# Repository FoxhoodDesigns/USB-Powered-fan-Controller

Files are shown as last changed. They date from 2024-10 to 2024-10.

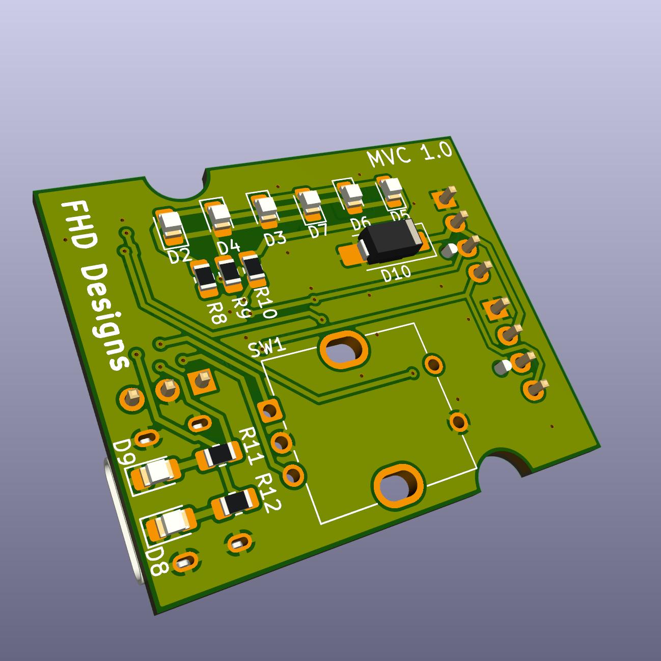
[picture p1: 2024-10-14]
KiCad/MVC.jpg

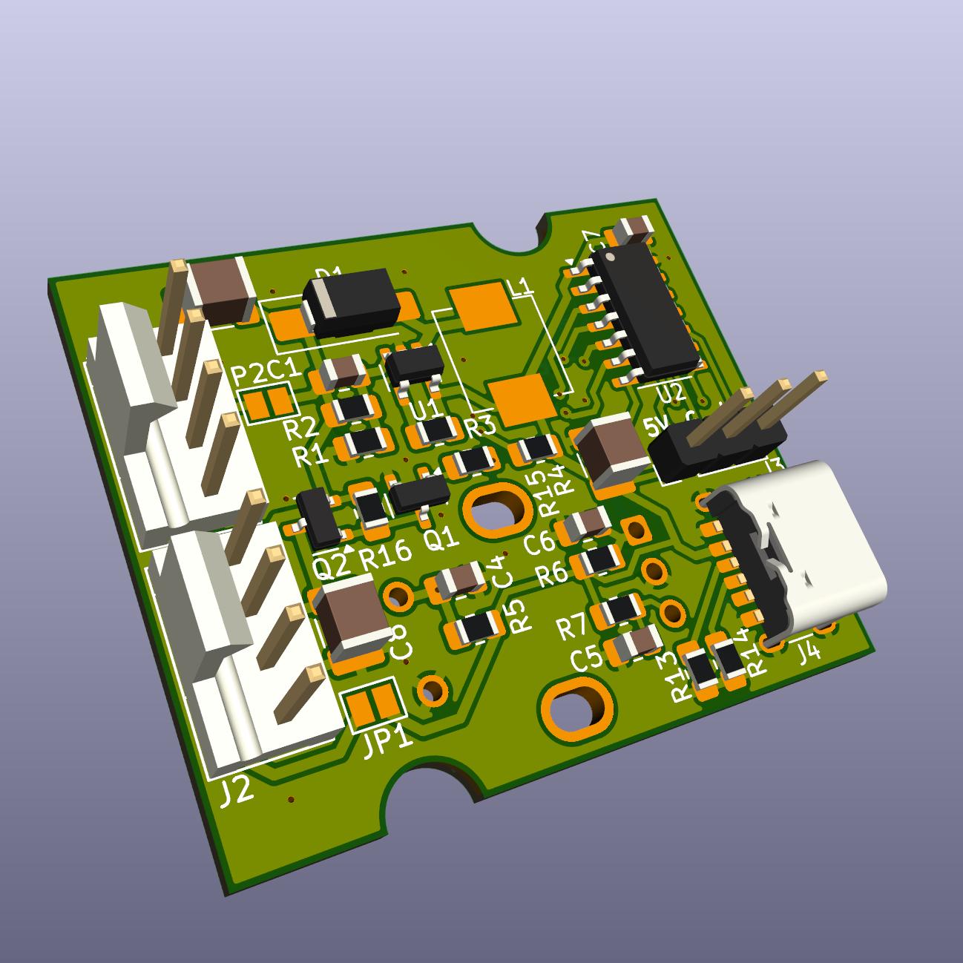
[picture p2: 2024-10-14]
KiCad/MVCfront.jpg

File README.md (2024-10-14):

# USB-Powered-fan Controller
This small device is designed to allow one to power and control a 12V (case)fan from a standard 5V 1A USB charger.
Intended application are small DIY fan projects such as a Desktop fan using a Noctua NV-AA1-12, Fume Extracters and Part cooling.
## Overal design:
The controller can be divided into four parts:
- A 5V->12V Boost converter based on a LMR62421XMF reference design
- A Load switch using a PMV50PEAR and a BSS138.
- A ATTiny414 that is handling PWM generation and I/O
- The I/O itself consisting of (charlieplexed) leds, Encoder, USB-C port and two 4-pin FAN pinouts
## Working
On power-up the controller will try to spin up the fan to about half speed via a 25Khz PWM signal, measure the RPM, set PWM to 80% and check if there was significant change.
If there was, then it assumes the FAN is PWM compatible and keep to using PWM, if not it will assume the FAN is DC and instead starts pulsing the Load Switch.

During operation one can set the speed of the fan anywhere between 40 and 100 percent. Pressing the encoder SW causes the controller to halt the fan till pressed again

If during operation the FAN either halts OR speeds up too much (wip), the controller will immediately shut off power and remain locked till it got power-cycled as a protection measure against sudden jamming/defects.

### TODO:
- Gerber upload
- Overhaul the code and implement a speed up detection test.
- Test with other fans.
- BOM upload
- Potentially setting up for manufacturing by PCBWay/JLCPCB
- Verify if possible to program via AVRDUDE using CH340

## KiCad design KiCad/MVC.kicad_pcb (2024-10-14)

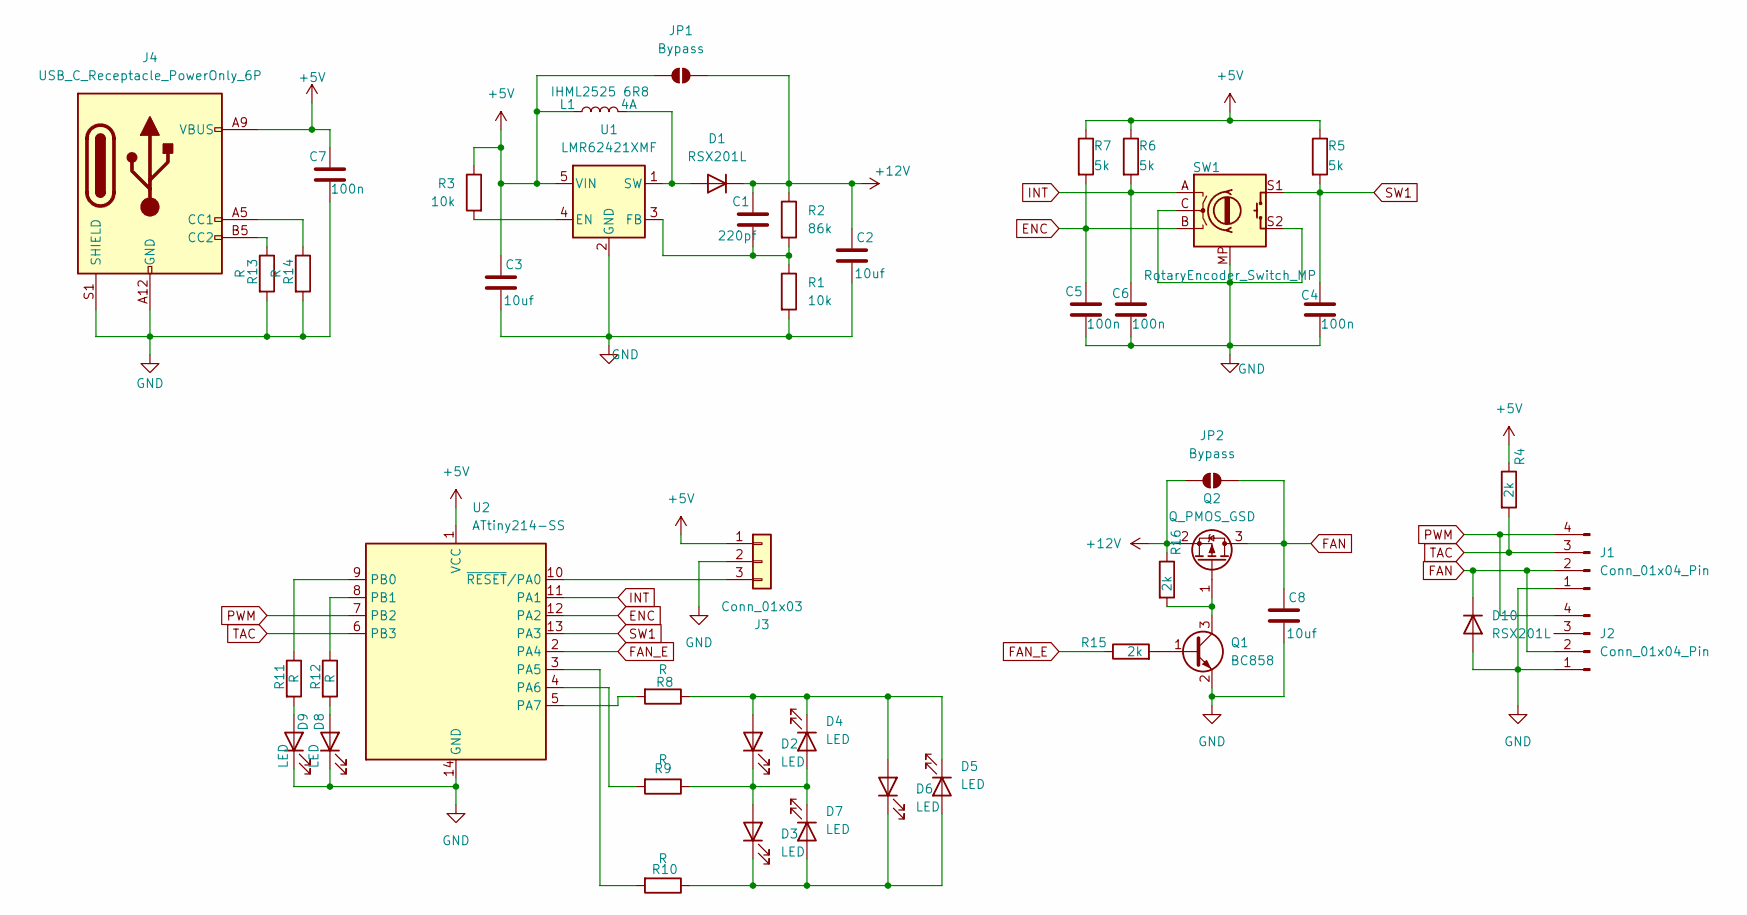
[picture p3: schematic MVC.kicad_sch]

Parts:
C1: 220pf; C_0805_2012Metric_Pad1.18x1.45mm_HandSolder; Voltage 1kV; Tolerance 100%
C2, C3, C8: 10uf; C_1210_3225Metric_Pad1.33x2.70mm_HandSolder; Voltage 1kV; Tolerance 100%
C4, C5, C6, C7: 100n; C_0805_2012Metric_Pad1.18x1.45mm_HandSolder; Voltage 1kV; Tolerance 100%
D1, D10: RSX201L; D_SMA_Handsoldering
D2, D3, D4, D5, D6, D7, D8, D9: LED; LED_0805_2012Metric_Pad1.15x1.40mm_HandSolder
J1, J2: Conn_01x04_Pin; FanPinHeader_1x04_P2.54mm_Vertical
J3: Conn_01x03; PinHeader_1x03_P2.54mm_Vertical
J4: USB_C_Receptacle_PowerOnly_6P; USB_C_Receptacle_GCT_USB4125-xx-x_6P_TopMnt_Horizontal
JP1, JP2: Bypass; SolderJumper-2_P1.3mm_Open_Pad1.0x1.5mm
L1: IHML2525 6R8; L_Vishay_IHLP-2525
Q1: BC858; SOT-23
Q2: Q_PMOS_GSD; SOT-23
R1, R3: 10k; R_0805_2012Metric_Pad1.20x1.40mm_HandSolder
R2: 86k; R_0805_2012Metric_Pad1.20x1.40mm_HandSolder
R4, R15, R16: 2k; R_0805_2012Metric_Pad1.20x1.40mm_HandSolder
R5, R6, R7: 5k; R_0805_2012Metric_Pad1.20x1.40mm_HandSolder
R8, R9, R10, R11, R12, R13, R14: R; R_0805_2012Metric_Pad1.20x1.40mm_HandSolder
SW1: RotaryEncoder_Switch_MP; RotaryEncoder_Bourns_Vertical_PEC12R-3x17F-Sxxxx
U1: LMR62421XMF; SOT-23-5
U2: ATtiny214-SS; SOIC-14_3.9x8.7mm_P1.27mm

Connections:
+5V: C3.1, C7.1, J3.1, J4.A9 (VBUS), J4.B9 (VBUS), JP1.1 (A), L1.1, R3.1, R4.1, R5.1, R6.1, R7.1, U1.5 (VIN), U2.1 (VCC)
+12V: C1.1, C2.1, D1.1 (K), JP1.2 (B), JP2.1 (A), Q2.2 (S), R2.1, R16.1
ENC: C5.1, R7.2, SW1.B, U2.12 (PA2)
FAN: C8.1, D10.1 (K), J1.2, J2.2, JP2.2 (B), Q2.3 (D)
FAN_E: R15.1, U2.2 (PA4)
GND: C2.2, C3.2, C4.2, C5.2, C6.2, C7.2, C8.2, D8.1 (K), D9.1 (K), D10.2 (A), J1.1, J2.1, J3.2, J4.A12 (GND), J4.B12 (GND), J4.S1 (SHIELD), Q1.2 (E), R1.2, R13.2, R14.2, SW1.C, SW1.MP, SW1.S2, U1.2 (GND), U2.14 (GND)
INT: C6.1, R6.2, SW1.A, U2.11 (PA1)
unnamed: D1.2 (A), L1.2, U1.1 (SW)
unnamed: D2.2 (A), D4.1 (K), D5.1 (K), D6.2 (A), R8.1
unnamed: D2.1 (K), D3.2 (A), D4.2 (A), D7.1 (K), R9.1
unnamed: D3.1 (K), D5.2 (A), D6.1 (K), D7.2 (A), R10.1
unnamed: D8.2 (A), R12.2
unnamed: D9.2 (A), R11.2
unnamed: J3.3, U2.10 (~RESET/PA0)
unnamed: J4.A5 (CC1), R14.1
unnamed: J4.B5 (CC2), R13.1
unnamed: Q1.1 (B), R15.2
unnamed: Q1.3 (C), Q2.1 (G), R16.2
unnamed: R3.2, U1.4 (EN)
unnamed: C1.2, R1.1, R2.2, U1.3 (FB)
unnamed: R10.2, U2.3 (PA5)
unnamed: R9.2, U2.4 (PA6)
unnamed: R8.2, U2.5 (PA7)
unnamed: R11.1, U2.9 (PB0)
unnamed: R12.1, U2.8 (PB1)
PWM: J1.4, J2.4, U2.7 (PB2)
SW1: C4.1, R5.2, SW1.S1, U2.13 (PA3)
TAC: J1.3, R4.2, U2.6 (PB3)

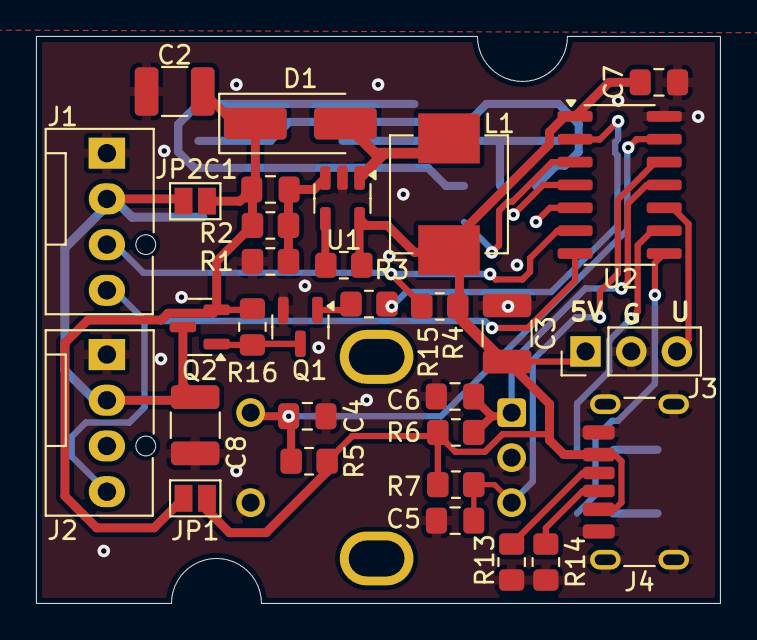
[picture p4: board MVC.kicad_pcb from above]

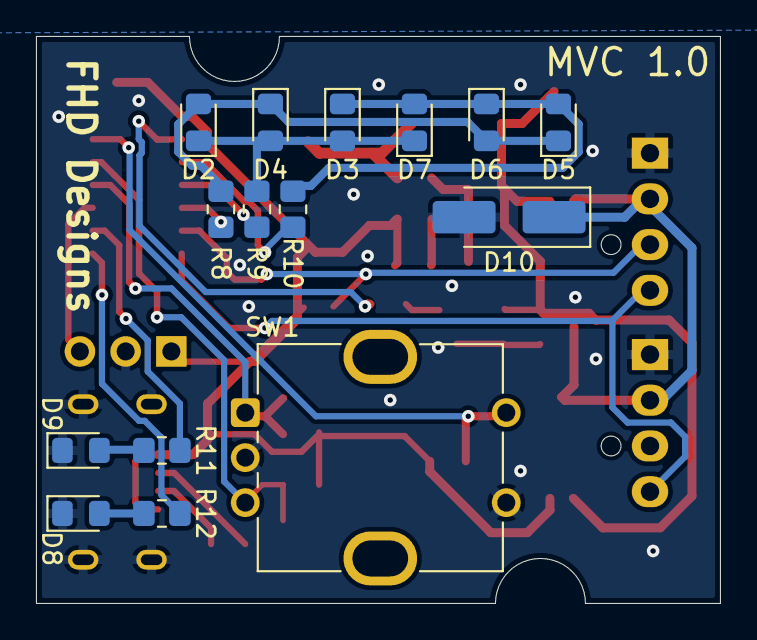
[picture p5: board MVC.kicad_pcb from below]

Board: 2 copper layers, 38.0 x 31.5 mm, 46 parts (15 on the bottom side), 28 nets.

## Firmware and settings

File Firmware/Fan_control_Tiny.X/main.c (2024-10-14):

/*
 * File:   main.c
 * Author: Foxhood
 *
 * Created on August 4, 2024, 11:35 PM
 */

//Reference cheat-sheet Read the IOTN1614.h file!

#define F_CPU   2500000UL
#include <avr/io.h>
#include <avr/interrupt.h>
#include <util/delay.h>


/* Pinout Cheat sheet:
 * B0: Green led
 * B1: Red led
 * B2: PWM
 * B3: TAC
 * A0: UPDI
 * A1: INT (Encoder)
 * A2: ENC (U/L)
 * A3: SW1
 * A4: FAN_E
 * A5: CP1
 * A6: CP2
 * A7: CP3 
 */

//Pin bitmasks
#define G_LED 0x01
#define R_LED 0x02
#define TAC 0x08
#define ENC 0x04
#define ENC_SW 0x08
#define FAN_E 0x10
#define PWM 0x04
//Macros
#define ERROR 0
#define DC_MODE 1
#define PWM_MODE 2
#define OFF_MODE 3


const uint8_t C_LED_OUT[6] = {0x04,0x02,0x02,0x01,0x04,0x01};
const uint8_t C_LED_DIR[6] = {0x06,0x06,0x03,0x03,0x05,0x05};
const uint8_t TMR_MAX_LIMIT = 100;
const uint8_t TMR_MIN_LIMIT = 40; //Set minimum speed to ~40%, 192 steps
const uint16_t TIMEOUT_limit = 1000;
const uint8_t Encoder_step = 5; //12 encoder steps to go from minimum to top speed
const uint8_t Led_step = 10;
volatile uint8_t set_speed = 50;
volatile uint16_t fan_rpm = 0;
volatile uint8_t time_out = 0;
volatile uint8_t state = 0;
volatile uint16_t pulse_width_counter = 0;
uint8_t fan_detect = PWM_MODE;
volatile uint8_t fan_mode = PWM_MODE;
uint8_t fan_stat;

uint8_t locked = 0;




//AVR Interrupt Service Routine
int led_out(uint8_t stat){
    if (stat == 0xff){
        PORTA.DIR = (PORTA.DIR & 0x1f);
        PORTA.OUT = (PORTA.OUT & 0x1f);
        return 1;
    }
    PORTA.OUT = (PORTA.OUT & 0x1f);
    PORTA.DIR = (PORTA.DIR & 0x1f) + (C_LED_DIR[stat]<<5);
    PORTA.OUT = (PORTA.OUT & 0x1f) + (C_LED_OUT[stat]<<5);
    return 0;
}
void led_bar_tick(uint8_t leds){
    static uint8_t ticker = 0;
    if (ticker < leds){
        led_out(ticker);
    } else {
        PORTA.DIR = (PORTA.DIR & 0x1f);
        //led_out(0xff);
    }
    ticker++;
    if (ticker == 6) ticker = 0;
}
ISR(PORTA_PORT_vect){
    if (PORTA.IN & ENC) {
        set_speed -= Encoder_step;
        if (set_speed < TMR_MIN_LIMIT) {
            set_speed = TMR_MIN_LIMIT;
        }
    } else {
        set_speed += Encoder_step;
        if (set_speed > TMR_MAX_LIMIT) {
            set_speed = TMR_MAX_LIMIT+1;
        }
    }
    if (fan_mode == PWM_MODE) {
        TCA0.SINGLE.CMP2 = set_speed;
    } else if (fan_mode == DC_MODE){
        TCA0.SPLIT.HCMP1 = set_speed << 1;
    }
    //led_out((set_speed-TMR_MIN_LIMIT)/Led_step);
    PORTA.INTFLAGS = 0xff;
}
ISR(TCB0_INT_vect){
    uint8_t input = (PORTB.IN & PIN3_bm);
    if (input == state){
        pulse_width_counter++;
    } else {
        fan_rpm = 1000 / pulse_width_counter * 15;
        pulse_width_counter = 0;
        state = input;
    }
    if (pulse_width_counter > TIMEOUT_limit && fan_mode != OFF_MODE) {
        time_out = 1;
    }
    TCB0.INTFLAGS = 1;
}

//Initiates timerA for output PWM generation.
//Target frequency is 25Khz. By dividing main 20Mhz clock by 8 (2.5Mhz) and using a period of 100. No division is needed.
void TCA_PWM_init(void) {
    TCA0.SINGLE.CTRLB = 0 << TCA_SINGLE_ALUPD_bp
	                    | 0 << TCA_SINGLE_CMP0EN_bp
	                    | 0 << TCA_SINGLE_CMP1EN_bp
	                    | 1 << TCA_SINGLE_CMP2EN_bp
	                    | TCA_SINGLE_WGMODE_SINGLESLOPE_gc;
    TCA0.SINGLE.PER = TMR_MAX_LIMIT;
    TCA0.SINGLE.CMP2 = TMR_MAX_LIMIT/2;
    TCA0.SINGLE.DBGCTRL = 1;
    TCA0.SINGLE.CTRLA = TCA_SINGLE_CLKSEL_DIV1_gc //set for 25khz
                        | 1 << TCA_SINGLE_ENABLE_bp;
}
//Reconfigures timerA for output DC generation.
void TCA_DC_init(void) {
    TCA0.SINGLE.CTRLA = 0;  //Disable from PWM mode
    TCA0.SINGLE.CMP2 = 0;
    TCA0.SPLIT.CTRLD = 1 << TCA_SPLIT_SPLITM_bp;
    TCA0.SPLIT.CTRLB =  1 << TCA_SPLIT_HCMP1EN_bp;
    TCA0.SPLIT.HPER = TMR_MAX_LIMIT*2;
    TCA0.SPLIT.HCMP1 = TMR_MAX_LIMIT;
    TCA0.SPLIT.CTRLA = TCA_SPLIT_CLKSEL_DIV1024_gc //set for lowest possible speed. (12.5hz)
                        | 1 << TCA_SPLIT_ENABLE_bp;
    PORTB.DIRSET = PWM;
    PORTB.OUTSET = PWM;    
}
//Initiates TimerB for tachometer monitoring. Sampling rate of 1Khz
void TCB_INT_int(void) {
    TCB0.INTCTRL = 1;
    TCB0.CCMP = 2500;
    TCB0.CTRLB = TCB_CNTMODE_INT_gc;
    TCB0.CTRLA = TCB_CLKSEL_CLKDIV1_gc | TCB_ENABLE_bm; //Enable with clkdiv1
}

//Initiates EVSYS and TimerB for Frequency measurement (FAILED TO GET WORKING...)
//https://github.com/microchip-pic-avr-examples/avr128da48-adc-evsys-example
/*
void evsys_timer_b_init(void) {
    //Activate EVSYS Event puss
    EVSYS.SYNCCH1 = EVSYS_SYNCCH1_PORTB_PIN2_gc; //Set Synchronous channel 1 to PORTB PIN3
    EVSYS.SYNCUSER0 = EVSYS_ASYNCUSER0_SYNCCH1_gc; //Set TCB User channel to Synchronous channel 1
    //EVSYS.SYNCCH1 = 0xb; //Set Synchronous channel 1 to PORTB PIN3
    //EVSYS.SYNCUSER0 = 0x2; //Set TCB User channel to Synchronous channel 1
    PORTB.DIRCLR = PIN3_bm;
    PORTB.PIN3CTRL = 0x00;
    TCB0.CTRLB = TCB_CNTMODE_CAPT_gc; //Set to Capture?
    //TCB0.EVCTRL = TCB_CAPTEI_bm | TCB_EDGE_bm;
    TCB0.DBGCTRL = 1;
    TCB0.INTCTRL = TCB_CAPT_bm;
    TCB0.CTRLA = 0x02 | TCB_ENABLE_bm; //Enable with clkdiv2
}*/

int main(void) {
    //set clock to 2.5Mhz
    CCP = 0xD8;
    CLKCTRL.MCLKCTRLB = CLKCTRL_PEN_bm | CLKCTRL_PDIV_8X_gc;    
    //Set IO
    PORTB.DIR = 0x07;    //Set B0-B2 as Output
    PORTA.DIR = 0xf0;    //set A4-A7 as Output
    //Start initial configuration
    PORTA.OUTSET = FAN_E;
    PORTA.PIN1CTRL = PORT_ISC_RISING_gc; //Set INT pin as Interrupt Source (Rising)
    TCA_PWM_init();
    TCB_INT_int();
    sei();
    //Fan Test. Run at half PWM speed for 4 seconds and record rpm
    PORTB.OUTSET = G_LED;
    TCA0.SINGLE.CMP2 = 50;
    _delay_ms(4000);
    uint16_t tach1 = fan_rpm;
    //Run at 80% speed for 4 seconds and test if higher than original * 1.33.
    PORTB.OUTCLR = G_LED;
    PORTB.OUTSET = R_LED;
    TCA0.SINGLE.CMP2 = 80;
    time_out = 0;
    _delay_ms(6000);
    //Configure based on result
    if (time_out == 1) {
        fan_detect = ERROR;
    } else if ((tach1 + (tach1/3)) < fan_rpm) {
        fan_detect = PWM_MODE;
        TCA0.SINGLE.CMP2 = set_speed;
    } else {
        fan_detect = DC_MODE;
    }
    
    //Prep main program
    if (fan_detect == PWM_MODE){
        fan_mode = PWM_MODE;
        PORTB.OUTSET = G_LED;
        PORTB.OUTCLR = R_LED;
    } else if (fan_detect == DC_MODE) {
        fan_mode = DC_MODE;
        TCA_DC_init();
        PORTB.OUTSET = R_LED | G_LED | 0x04; //Turn on both leds and set PWM pin to always on.
    } else {
        fan_mode = ERROR;
    }
    _delay_ms(500);
    time_out = 0; //reset for run-time
    while(1) {
        switch(fan_mode){
            case DC_MODE:
                if (!(PORTA.IN & ENC_SW)) { //Switch to off
                    fan_mode = OFF_MODE;
                    TCA0.SPLIT.HCMP1 = 0;
                    PORTA.OUTCLR = FAN_E;
                    PORTB.OUTCLR = G_LED | R_LED;
                    led_out(0xff);
                    _delay_ms(1000);
                }
                if (time_out) {
                    fan_mode = ERROR;
                }
                led_bar_tick((set_speed-TMR_MIN_LIMIT)/Led_step);
                break;
            case PWM_MODE:
                if (!(PORTA.IN & ENC_SW)) { //Switch to off
                    fan_mode = OFF_MODE;
                    TCA0.SINGLE.CMP2 = 0;
                    PORTA.OUTCLR = FAN_E;
                    PORTB.OUTCLR = G_LED | R_LED;
                    led_out(0xff);
                    _delay_ms(1000);
                }
                if (time_out) {
                    fan_mode = ERROR;
                }
                led_bar_tick((set_speed-TMR_MIN_LIMIT)/Led_step);
                break;
            case OFF_MODE:
                led_out(0xff);
                if (!(PORTA.IN & ENC_SW)) { //Switch to ON
                    if (fan_detect == PWM_MODE){
                        fan_mode = PWM_MODE;
                        PORTB.OUTSET = G_LED;
                        TCA0.SINGLE.CMP2 = set_speed;
                    } else {
                        fan_mode = DC_MODE;
                        PORTB.OUTSET = G_LED | R_LED;
                        TCA0.SPLIT.HCMP1 = set_speed * 2;
                    }
                    PORTA.OUTSET = FAN_E;
                    
                    
                    _delay_ms(1000);
                    time_out = 0;
                }
                break;
            default: //Error
                if (!locked) {
                    cli();  //Shut off interrupt
                    TCA0.SINGLE.CTRLA = 0;  //Shut off Timer
                    TCB0.CTRLA = 0;
                    PORTA.OUTCLR = FAN_E;
                    PORTA.DIR = 0;  //Disable all outputs except for the status leds
                    PORTB.DIR = 0x03;
                    locked = 1;
                }
                while(1) {
                    PORTB.OUTSET = G_LED | R_LED;
                    _delay_ms(1000);
                    PORTB.OUTCLR = G_LED | R_LED;
                    _delay_ms(1000);
                }
                break;
        }
        _delay_us(100);       
    }
}
